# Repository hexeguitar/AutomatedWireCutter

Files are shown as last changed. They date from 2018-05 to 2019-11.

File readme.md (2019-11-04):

Automated Wire Cutter
========

PSoC4200 based wire cutter with remote console command interface.
[Link to project build page](https://www.hexefx.com/diy/utility/wirecut)

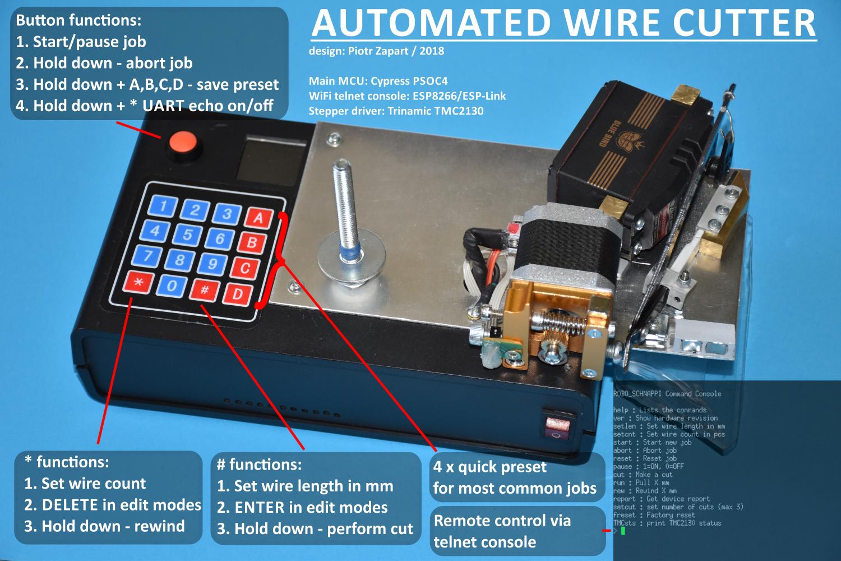
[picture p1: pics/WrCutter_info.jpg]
  

------

#### Project file tree:
* hardware: KiCad project, BOM, PCB assembly guide, gerber files
* software: PSoC Creator 4.2 project, compiled hex file
* pics  

#### Hardware:  
* PSoC4200 CY8C4245AXI-483 - main MCU
* ESP8266 (ESP12 module) - used as serial/Wifi bridge, pin header for CP2102 based programmer, auto bootloader mode via single DTR line
* Cypress PROC EZ-BLE module  - optional
* IR wire presence detector
* 128x128 SPI ST7735 display  
* 4x4 Keypad
* Trinamic TMC2130 Silent Step Stick stepper controller
* A4988 stepper driver (optional)
* PCB designed as development platform with prototyping area, LEDs, etc.

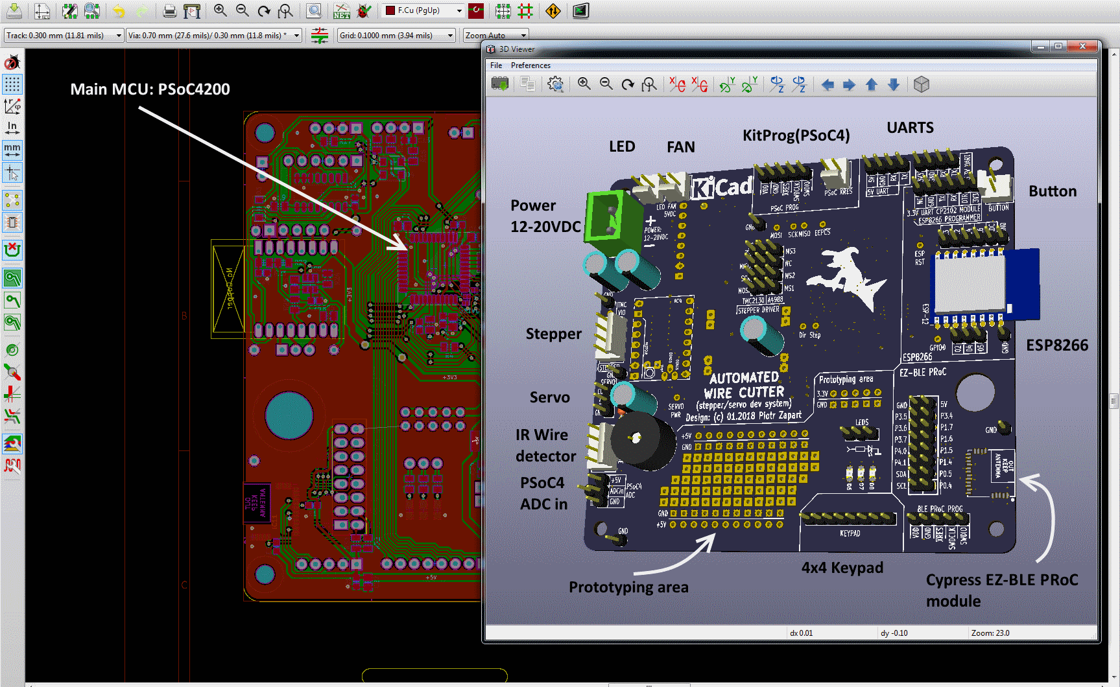
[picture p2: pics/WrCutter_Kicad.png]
  

Demo video:  

AutomatedWireCutter (http://www.youtube.com/watch?v=adL4IQJYwPY)

------
#### Software:  
- Firmware for the PSoC has been written in C using the PSoC Creator 4.2.  
- ESP8266 runs [ESP-link](https://github.com/jeelabs/esp-link) firmware and serves as Wifi/Serial bridge over telnet or via built in web server.  

------
#### Serial/telnet console:

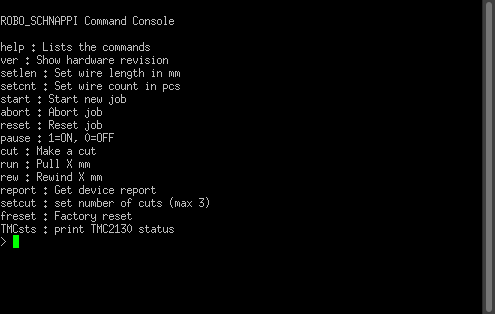
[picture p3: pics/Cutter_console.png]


------

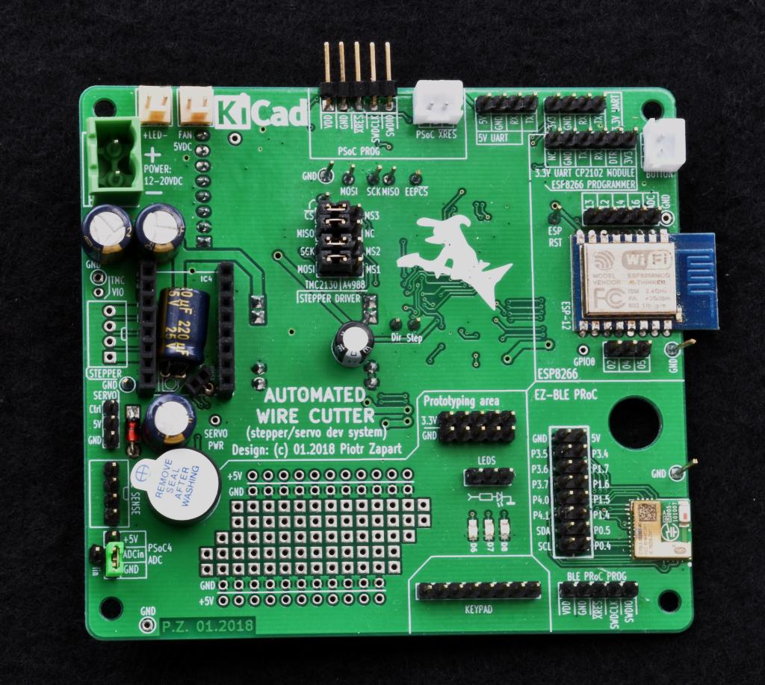
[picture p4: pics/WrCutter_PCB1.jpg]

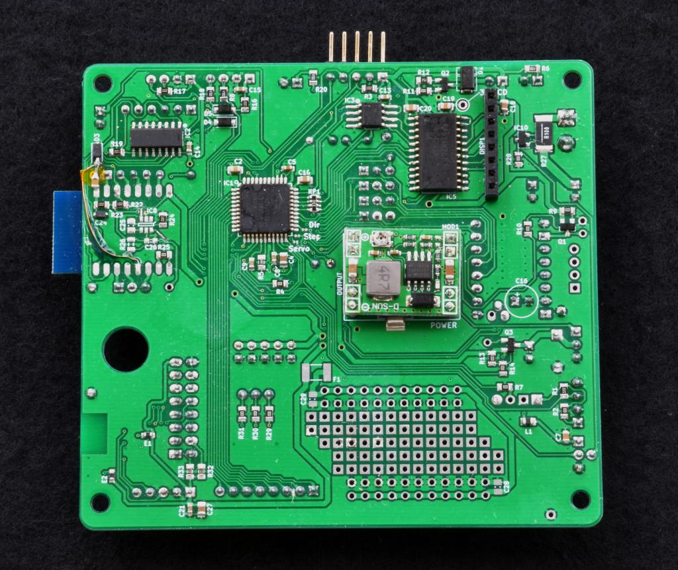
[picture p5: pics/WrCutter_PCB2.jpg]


------
(c) 05.2018 by Piotr Zapart  
www.hexefx.com 

[pic1]: pics/WrCutter_info.jpg "Automated Wire Cutter"

[pic2]: pics/WrCutter_Kicad.png "Kicad project"
[pic3]: pics/WrCutter_PCB1.jpg "Wire Cutter PCB"
[pic4]: pics/WrCutter_PCB2.jpg "Wire Cutter PCB"
[pic5]: pics/Cutter_console.png "Console"
[pic6]: pics/PulseAnim2.gif "UART as stepper driver"

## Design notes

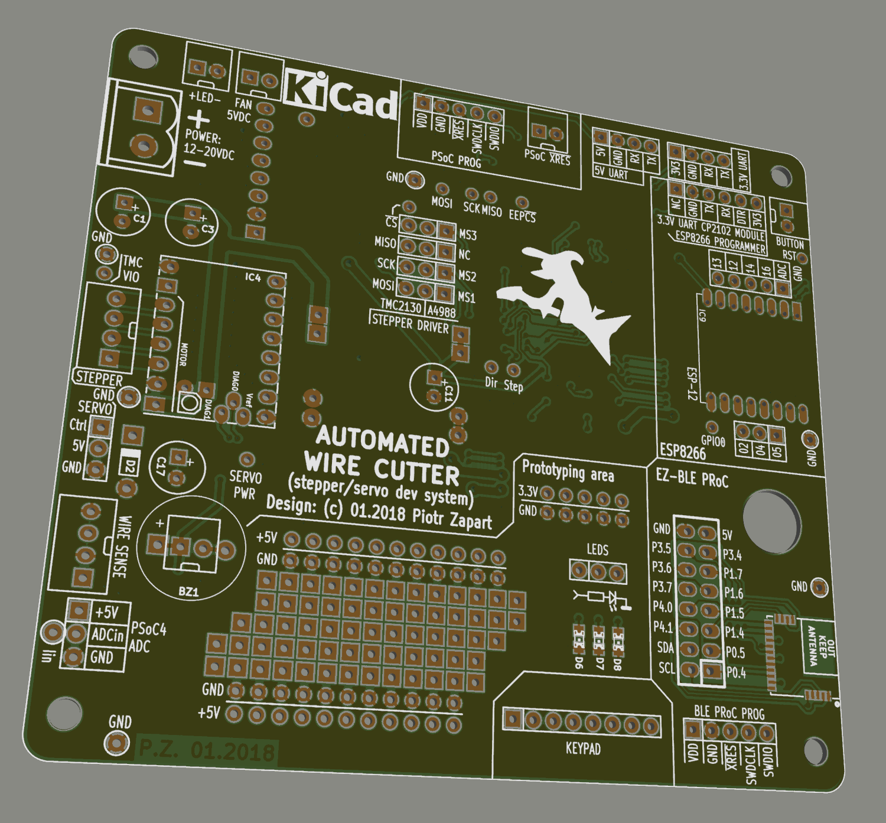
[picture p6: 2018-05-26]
hardware/gerbers/WireCutter_render.png

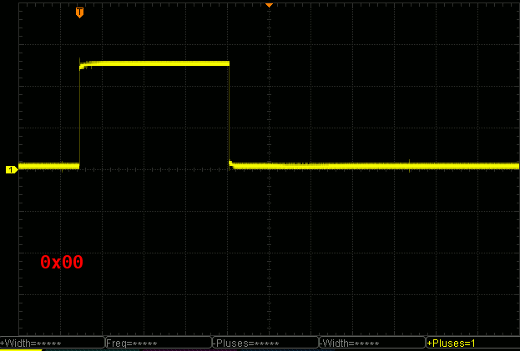
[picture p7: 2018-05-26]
pics/PulseAnim2.gif

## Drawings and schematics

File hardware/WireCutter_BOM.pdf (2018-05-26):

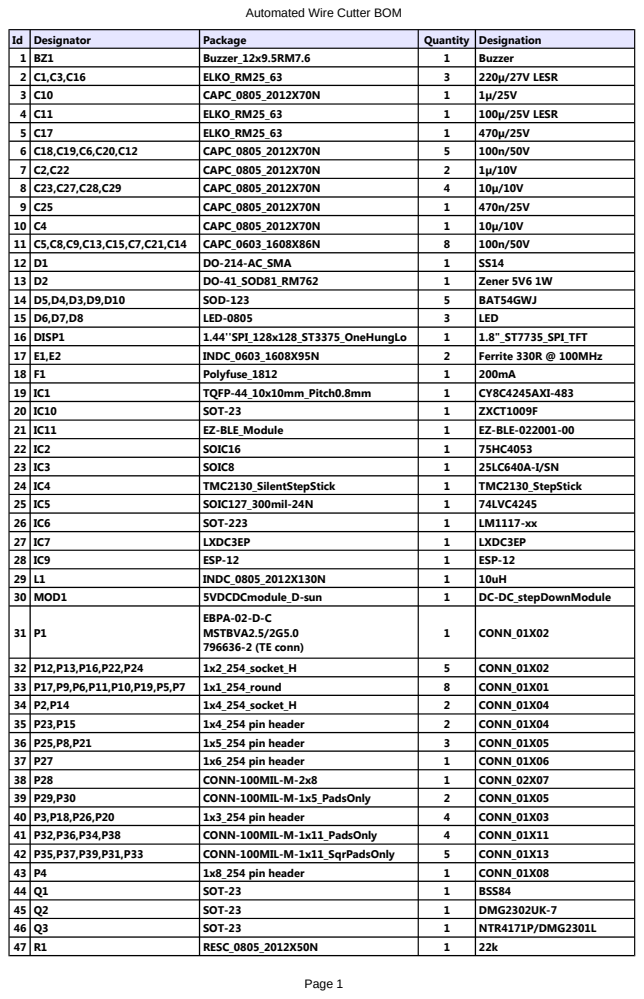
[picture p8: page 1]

Automated Wire Cutter BOM

Automated Wire Cutter BOM

48 | RESC_0805_2012X50N | 11 | 1k
49 | RESC_0805_2012X50N | 10 | 10k
50 R12 | RESC_0805_2012X50N | 1 | 150R
51 R13,R9 | RESC_0805_2012X50N | 2 | 100k
52 R27 | RESC_2512 | 1 | 0.1R 1-3W-current sensing
53 R32,R33 | RESC_0805_2012X50N | 2 | 1k5
54 R5 | RESC_0805_2012X50N | 1 | 33R
55 R6 | RESC_0805_2012X50N | 1 | 330R
56 R8,R18,R20 | RESC_0805_2012X50N | 3 | 470R
57 RP1 | R_Array_Convex_4x0603 | 1 | 33R
58 SW1 | 1x3_254 pin header | 1 | MISO/RST
59 SW2 | 1x3_254 pin header | 1 | ~CS~/MS3
60 SW3 | 1x3_254 pin header | 1 | SCK/MS2
61 SW4 | 1x3_254 pin header | 1 | MOSI/MS1
62 | Stepper motor | 1 | NEMA 42HD4027-01
63 | Extruder kit | 1
64 | Servo | | BMS-L530MG

R10,R2,R4,R7,R14,R21,R25,
R28,R29,R30,R31
R11,R3,R15,R16,R17,R19,
R22,R23,R26,R24

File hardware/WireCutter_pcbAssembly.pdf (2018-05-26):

# Automated Wire Cutter PCB assembly

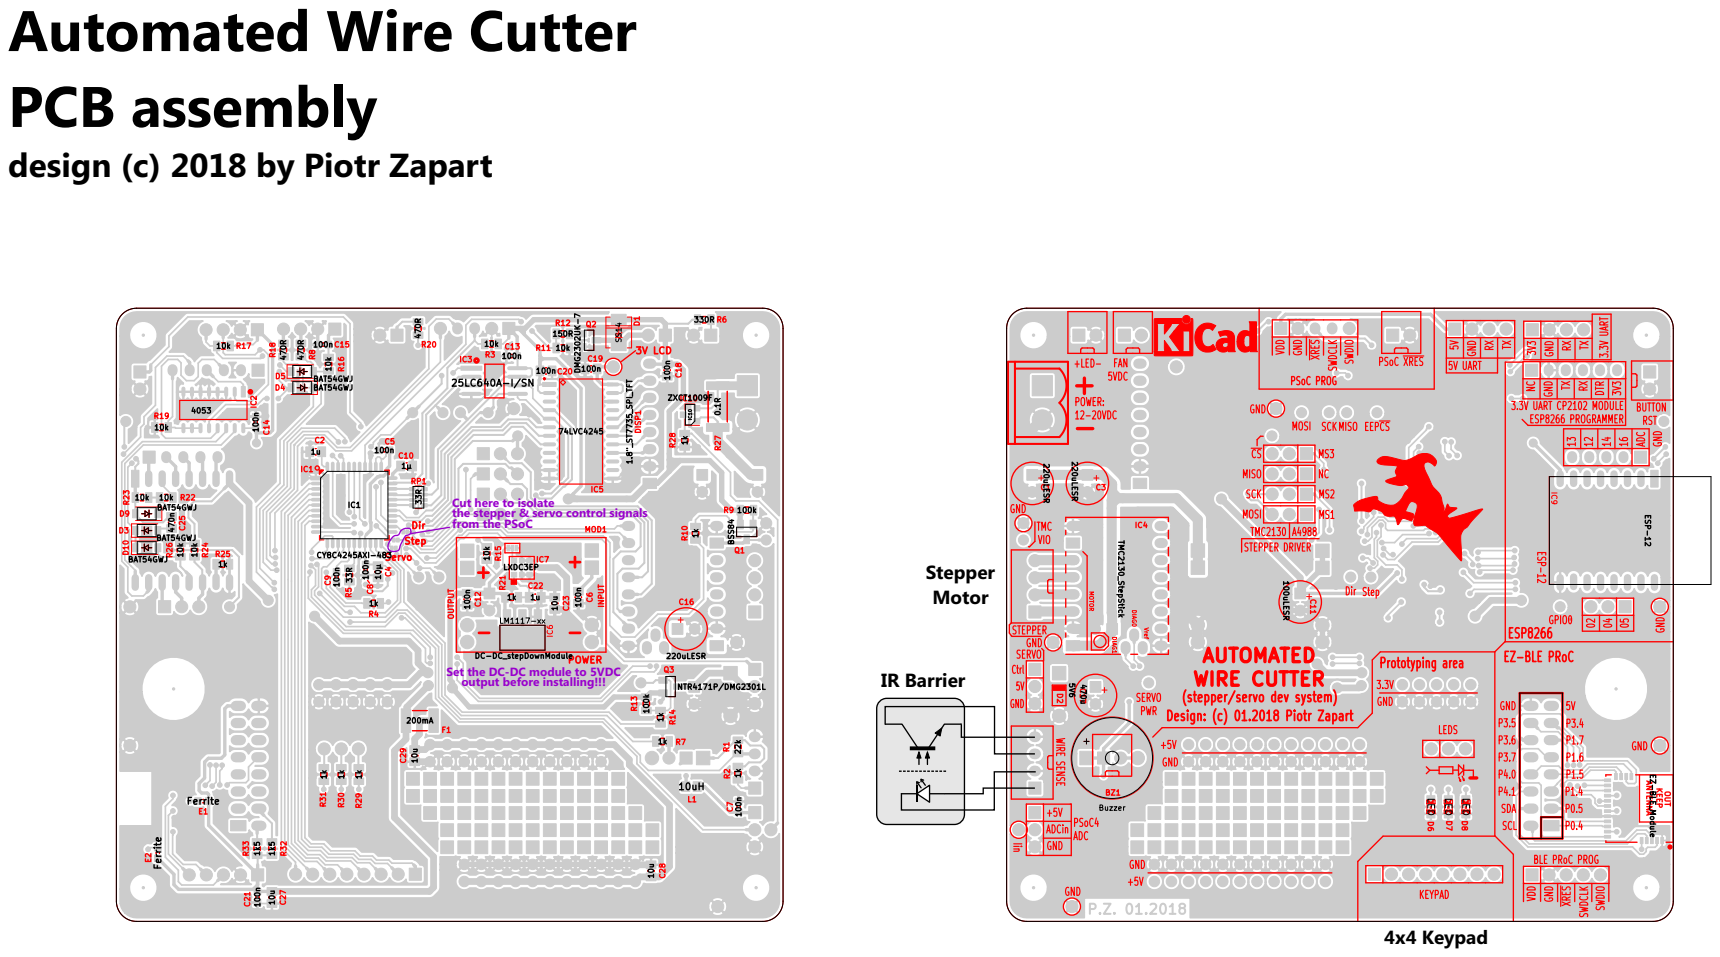
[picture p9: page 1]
4x4 Keypad; Stepper Motor

design (c) 2018 by Piotr Zapart

Cut here to isolate
the stepper & servo control signals
from the PSoC

IR Barrier Set the DC-DC module to 5VDC
output before installing!!!

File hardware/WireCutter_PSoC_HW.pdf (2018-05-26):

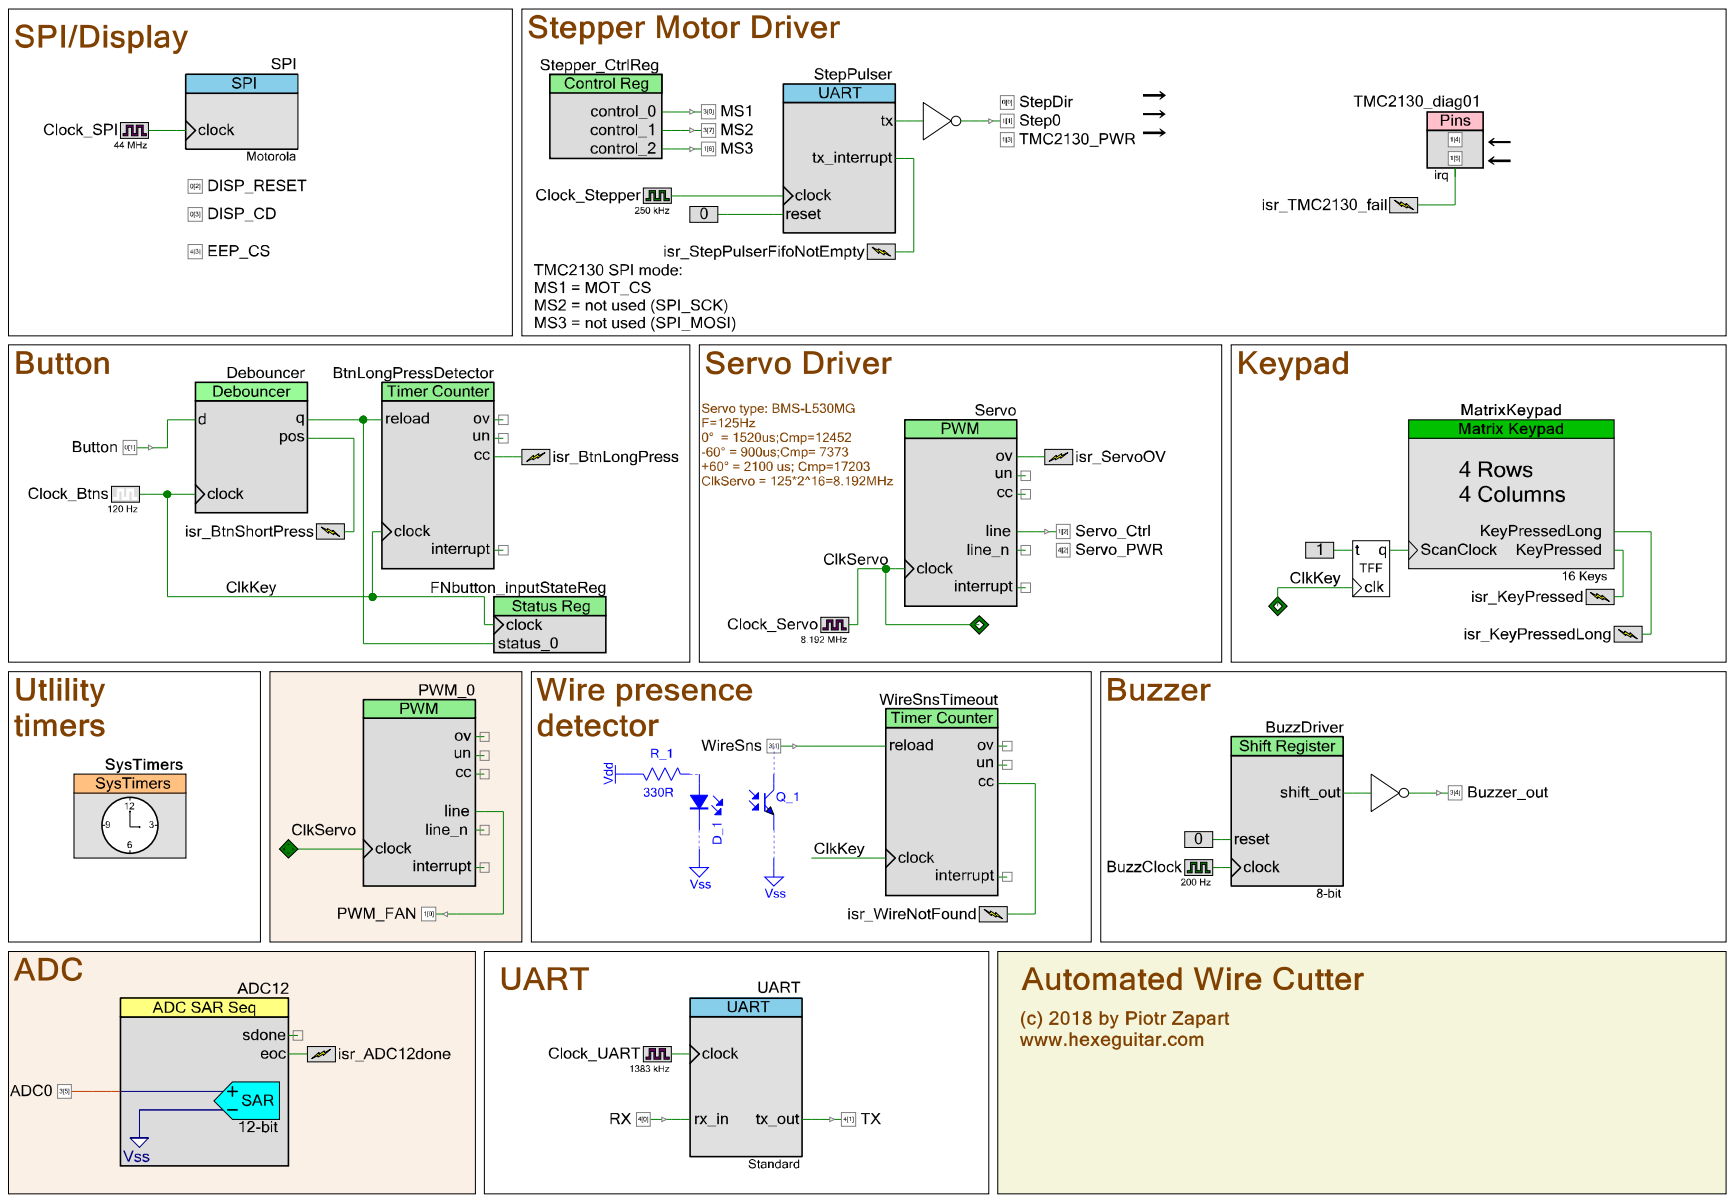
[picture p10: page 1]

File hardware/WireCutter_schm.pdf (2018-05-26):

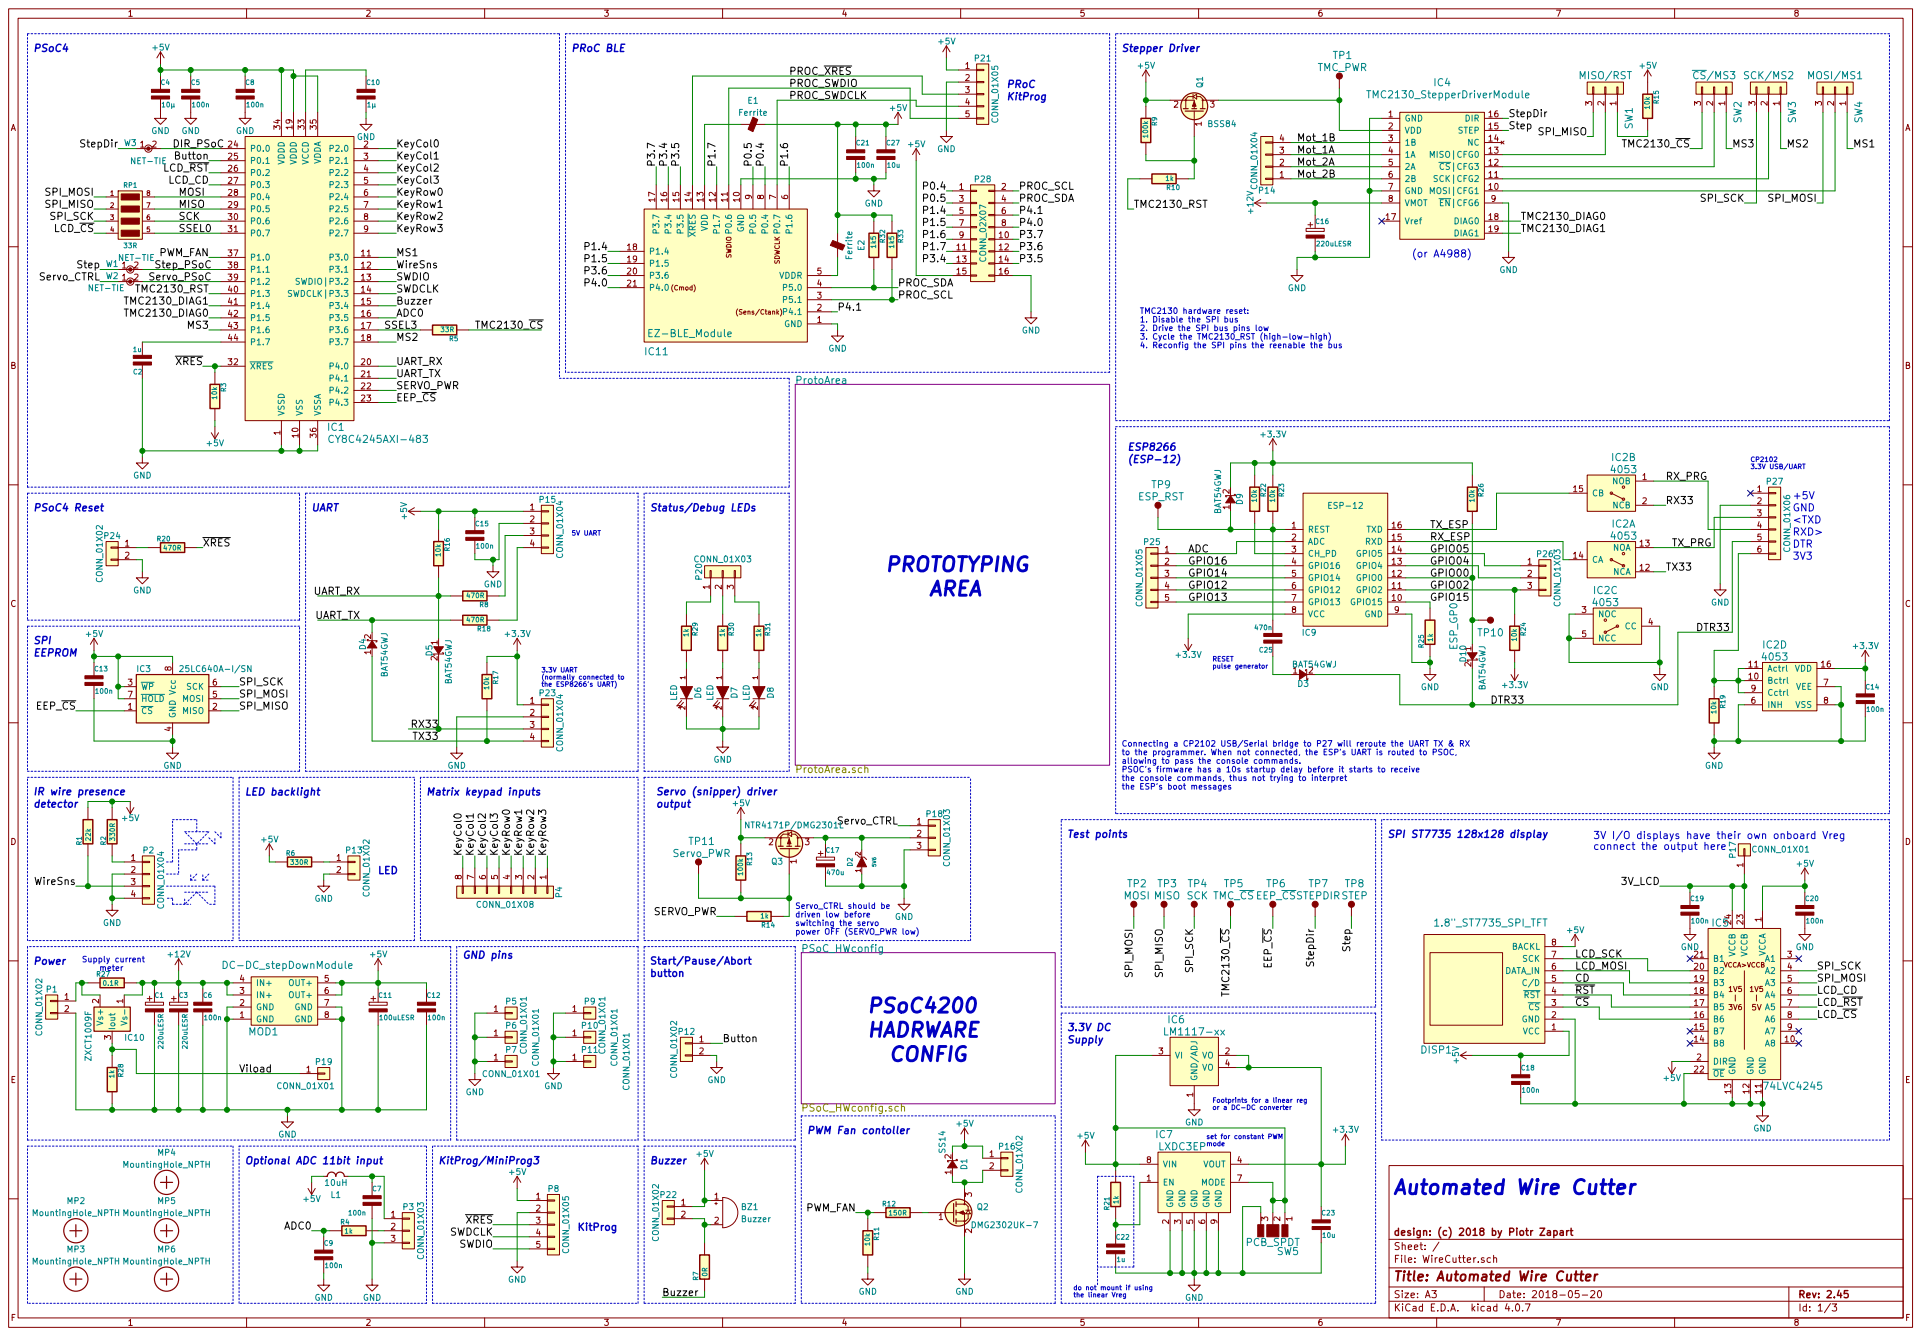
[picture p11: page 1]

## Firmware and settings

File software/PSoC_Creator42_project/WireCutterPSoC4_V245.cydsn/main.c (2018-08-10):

/*
 * Copyright (c) 2018 by Piotr Zapart / www.hexeguitar.com
 *
 * All rights reserved.
 *
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
 * Neither the name of the Piotr Zapart or HEXE Guitar Electronics nor the names of its 
 * contributors may be used to endorse or promote products derived from this software 
 * without specific prior written permission.
 * 
 * THIS SOFTWARE IS PROVIDED BY THE COPYRIGHT HOLDERS AND CONTRIBUTORS "AS IS" 
 * AND ANY EXPRESS OR IMPLIED WARRANTIES, INCLUDING, BUT NOT LIMITED TO, THE IMPLIED 
 * WARRANTIES OF MERCHANTABILITY AND FITNESS FOR A PARTICULAR PURPOSE ARE DISCLAIMED. 
 * IN NO EVENT SHALL THE COPYRIGHT HOLDER OR CONTRIBUTORS BE LIABLE FOR ANY DIRECT, 
 * INDIRECT, INCIDENTAL, SPECIAL, EXEMPLARY, OR CONSEQUENTIAL DAMAGES (INCLUDING, BUT 
 * NOT LIMITED TO, PROCUREMENT OF SUBSTITUTE GOODS OR SERVICES; LOSS OF USE, DATA, 
 * OR PROFITS; OR BUSINESS INTERRUPTION) HOWEVER CAUSED AND ON ANY THEORY OF LIABILITY, 
 * WHETHER IN CONTRACT, STRICT LIABILITY, OR TORT (INCLUDING NEGLIGENCE OR OTHERWISE) 
 * ARISING IN ANY WAY OUT OF THE USE OF THIS SOFTWARE, EVEN IF ADVISED OF THE POSSIBILITY
 * OF SUCH DAMAGE.
 */
#include <project.h>
#include "ugui.h"
#include "ugui_st7735.h"
#include "gui.h"
#include "keypad.h"
#include "FNbutton.h"
#include "tinyprintf.h"
#include "utils.h"
#include "StepperDriver.h"
#include "ServoDriver.h"
#include "debug.h"
#include "engine.h"
#include "TMC2130.h"
#include "TMC2130_reg.h"
#include "buzzer.h"
#include "console.h"
#include "adc.h"
#include "config.h"



// #############################################################################
// #### Global variables ###

// #############################################################################
// ### Function declarations ###


// #############################################################################
int main(void)
{
    CyGlobalIntEnable; /* Enable global interrupts. */

    UART_Start();
    
    init_printf(NULL,putChar);
    SysTimers_Start();
      
    EEP_CS_Write(1);    
    SPI_Start();
    SPI_SpiSetActiveSlaveSelect(SPI_SPI_SLAVE_SELECT0); //select display
    gui_init();
    keypad_init();
    FNbutton_init();
    Buzzer_init();
    engineInit();
    ConsoleInit();
    
    //Servo_enableCut(0);   //the cut operation can be optionally disabled (ie for testing)
    
    PWM_0_Start();
    
    ADC_init();
    
    //configure watchdog
    CySysWdtWriteMode(CY_SYS_WDT_COUNTER0,CY_SYS_WDT_MODE_RESET);   //counter 0 reset mode
    
    CySysWdtWriteMatch(CY_SYS_WDT_COUNTER0,0xFFFF);                 //
    CySysWdtWriteClearOnMatch(CY_SYS_WDT_COUNTER0, 1u);
    #ifndef DEBUG_ENABLED
    CySysWdtEnable(CY_SYS_WDT_COUNTER0_MASK);                       //enable counter 0
    #endif
    
    for(;;)
    {
        //clear the watchdog counter
        CySysWdtResetCounters(CY_SYS_WDT_COUNTER0_RESET);
        
        if (SysTimers_GetSysTickValue() > 10000ul)  // startup delay 10s - ESP8266 boot messages 
        {
            ConsoleProcess();
        }
        else
        {
            while (UART_SpiUartGetRxBufferSize() > 0)
            {
                 UART_UartGetChar();                //just read the incoming data to flush out the buffer
            }
        }

        //engine_checkButtons();
        Buzzer_handler();       
        doYourJob();            //main engine handler
    }
}

/* [] END OF FILE */

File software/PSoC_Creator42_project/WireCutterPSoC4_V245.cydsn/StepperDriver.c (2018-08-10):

/*
 * Copyright (c) 2018 by Piotr Zapart / www.hexeguitar.com
 *
 * All rights reserved.
 *
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
 * Neither the name of the Piotr Zapart or HEXE Guitar Electronics nor the names of its 
 * contributors may be used to endorse or promote products derived from this software 
 * without specific prior written permission.
 * 
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
 */
#include <project.h>
#include "StepperDriver.h"
#include "tinyprintf.h"
#ifdef USE_TMC2130
    #include "TMC2130.h"
#endif
#include "A4988.h"
#include "config.h"
#include "debug.h"

const uint8_t fullPulseByte = 0x55;
const uint8_t partialPulseBytes[4]=
{
    0x00,   //1 puse 
    0x01,   //2 pulses
    0x05,   //3 pulses
    0x15    //4 pulses
};

#ifdef USE_TMC2130
TMC2130_t Stepper0;
#endif
// ### Global variables ###

Stepper_drvType_t Stepper_driverType = STPDRV_A4988;    //assume TMC2130 is not present

static volatile uint32_t _fullBytesToSend = 0;
static volatile uint8_t _lastByteToSend = 0;
uint16_t Stepper_defaultClockDivider;
uint8_t Stepper_defaultClockDividerFrac;

static volatile uint32_t Stepper_fullBytesJob;
static volatile uint32_t Stepper_clkDiv;
volatile int16_t Stepper_driverTemp = 0; 

static volatile uint8_t Stepper_pauseFlag = 0; 

StepperStatus_t Stepper0_Status;

uint32_t Stepper_usteps = 0;

// ### Function declarations ###
CY_ISR_PROTO(PulserFifoNotEmpty_ISR);

void Stepper_sendPulses(void);



// ### Function definitions ###
// #############################################################################

CY_ISR (PulserFifoNotEmpty_ISR)
{
    static uint32_t Stepper_clkDiv_old = 0;
    #ifdef STEPPER_USE_RAMP
        // ramp up
        if (_fullBytesToSend > Stepper_fullBytesJob-STEPPER_RAMP_TIME)
        {
            if (Stepper_clkDiv > STEPPER_CRUISE_SPEED)  Stepper_clkDiv -=STEPPER_SPEED_DELTA;
            else                                        Stepper_clkDiv = STEPPER_CRUISE_SPEED;         
        }
        // ramp down
        if (_fullBytesToSend <= STEPPER_RAMP_TIME && Stepper_clkDiv < STEPPER_SLOW_SPEED)
        {
            Stepper_clkDiv +=STEPPER_SPEED_DELTA;
        }

        if (Stepper_clkDiv != Stepper_clkDiv_old)
        {
            Clock_Stepper_SetDivider(Stepper_clkDiv);
            Stepper_clkDiv_old = Stepper_clkDiv;
        }
    #endif
    if (Stepper_pauseFlag)
    {
        Stepper_pauseFlag = 0;
        StepPulser_DisableTxInt();
    }
    else
    {
        if (_fullBytesToSend)                            //if there are sill full pulse-bytes to send
        {
            StepPulser_PutChar(fullPulseByte);
            _fullBytesToSend--;
        }
        else
        {
            if (Stepper0_Status == STPDRV_RUNNING)  
            {
                if (_lastByteToSend)  StepPulser_PutChar(partialPulseBytes[_lastByteToSend-1]);
                Stepper0_Status = STPDRV_IDLE;     //job done
            }
            else    StepPulser_DisableTxInt();          //disable the interrupt
        }

    }
}

/*****************************************************************************\
 * Function:    Stepper_init
 * Input:       none
 * Returns:     none
 * Description: 
 *     Steps the motor
\*****************************************************************************/
void Stepper_init(void)
{    
    #ifdef STEPPER_USE_RAMP
    Clock_Stepper_SetDivider(STEPPER_SLOW_SPEED);
    #else
    Clock_Stepper_SetDivider(STEPPER_CRUISE_SPEED);    
    #endif
    
    // in order to HE reset the TMC130 the SPI has to be disabled and the pins driven with 0
    // to avoid powering the chip via input protection diodes.    
    SPI_Stop();         
    SPI_sclk_m_Write(0);
    SPI_miso_m_Write(0);
    SPI_mosi_m_Write(0);
    SPI_ss1_m_Write(0);        
    TMC2130_PWR_Write(1);   //power off
    CyDelay(100);
    TMC2130_PWR_Write(0);   //power on    
    CyDelay(100);    
    SPI_Start();            // restart the SPI
    TMC2130_set_device(&Stepper0);                                  //set the device to 0
    Stepper0.slaveSelect = TMC2130_SPI_SLAVE_SELECT;                //set the chip select line
    
    // detect the TMC2130 presence by reading DRV_STATUS, it the read returns 0xFFFFFFFF - assume the TMC is not present
    if (TMC2130_getDRV_STATUS() != 0xFFFFFFFF) 
    {
        Stepper_driverType = STPDRV_TMC2130;    
        Stepper_usteps = MICROSTEPS;    
        
        TMC2130_init(   &Stepper0,  //pointer to the motor struct
                        MICROSTEPS, //microsteps
                        1000,       //Irun = 1.0A
                        20,         //Ihold = 0% Irun
                        110,        //Rsense = 0R110
                        0);         //Stealth mode
    }
    else    // A4988 microstepping control - max value = 16, update the global value if required
    {
        Stepper_usteps = A4988_setUsteps(MICROSTEPS);
    }
    
    StepDir_Write(STEPPER_ROT_FWD);
    
    StepPulser_Start();
    StepPulser_DisableTxInt();                      //will be enabled in "startStepping" function
    isr_StepPulserFifoNotEmpty_ClearPending();
    isr_StepPulserFifoNotEmpty_StartEx(PulserFifoNotEmpty_ISR);

    Stepper0_Status = STPDRV_IDLE;  
}

/*****************************************************************************\
 * Function:    Stepper_getDriverType
 * Input:       none
 * Returns:     Stepper_driverType
 * Description: 
 *      returns the current detected (TMC2130) or default assumed stepper
 *      driver type
\*****************************************************************************/
Stepper_drvType_t Stepper_getDriverType(void)
{
    return Stepper_driverType;
}

/*****************************************************************************\
 * Function:    Stepper_getUsteps
 * Input:       none
 * Returns:     Current usteps value
 * Description: 
\*****************************************************************************/
uint8_t Stepper_getUsteps(void)
{
    return Stepper_usteps;
}

/*****************************************************************************\
 * Function:    Stepper_reset
 * Input:       none
 * Returns:     none
 * Description: 
 *     Performs a hardware reset of the stepper driver by toggling the power
\*****************************************************************************/
void Stepper_reset(void)
{
    TMC2130_PWR_Write(1);   //power off   
    CyDelay(10);
    TMC2130_PWR_Write(1);   //power on
    CyDelay(10);
}

/*****************************************************************************\
 * Function:    Stepper_runSteps
 * Input:       number of steps
 * Returns:     status
 * Description: 
 *     Steps the motor
\*****************************************************************************/
void Stepper_runSteps(uint32_t steps)
{
    if (Stepper0_Status==STPDRV_RUNNING) return;

    _fullBytesToSend = steps / 5;
    _lastByteToSend = steps % 5;
    Stepper_fullBytesJob = _fullBytesToSend;

    Stepper_sendPulses(); 
}
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
